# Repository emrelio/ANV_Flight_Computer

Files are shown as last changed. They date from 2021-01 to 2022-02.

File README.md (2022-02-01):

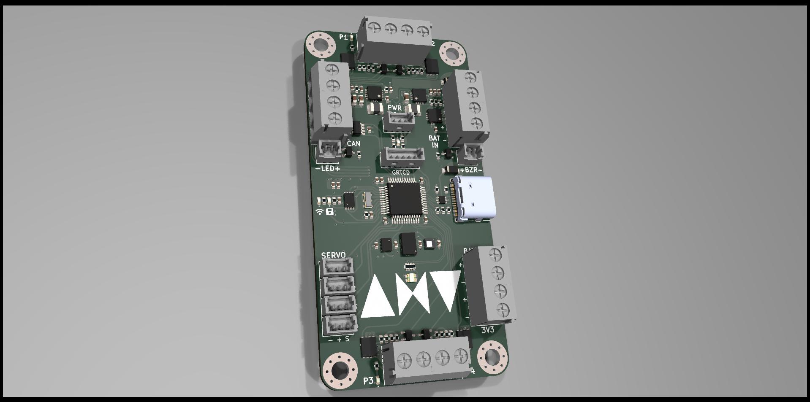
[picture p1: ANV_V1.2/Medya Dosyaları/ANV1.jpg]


Flight computer design for experimental model rocket flights.

I design this PCB for TVC of low power rockets.

Specs:

3-12V battery input,
  
Reverse battery protection,
  
3.3V and 5V switching regulators,
  
One main arm switch connector to cut all the power from the board,
  
Magnetic Switch connector for activation,
  
4, high current logic outputs,
  
All high current outputs have feedback for continuity detection,
  
4, 5v Servo outputs,
  
1,  LED and 1, active Buzzer connector,
  
1, RGB LED for notification,
  
ARM MCU,
  
Battery voltage and current sensors,
  
2, barometer from different brands for reliability,
  
9 DOF IMU,
  
4MB of memory for data logging,
  
Type-C connector for reading logged data,
  
433mHz LoRa for long-range wireless communication with U.FL connection,
  
Notification LED's for memory write and wireless communication,
  
Notification LED's for each high current outputs,
  
Screw terminal connector for power in-outs,
  
CAN-Bus connector for expansions in future,
  
M3 screw holes are connected to (BATT+, BATT-(GND), CAN-H, CAN-L).

Designed in KiCAD nightly.

Log:
  
Hall effect sensor out pin needs pull-up resistor, not pull-down. So It doesn't work.  
3.3V regulator acting abnormally. I might overheated it while soldering. Will try it on another board.  
IMU and Barometers are working.  
USB VCP is working.  
Current sensor is working.  
Mosfet feedback is working.  
Flash memory is working, logging algorithm is ready.  
Servo is working with integrated 5V regulator. Voltage might drop on load.  
  
To-Do :

Lora  
Can-Bus

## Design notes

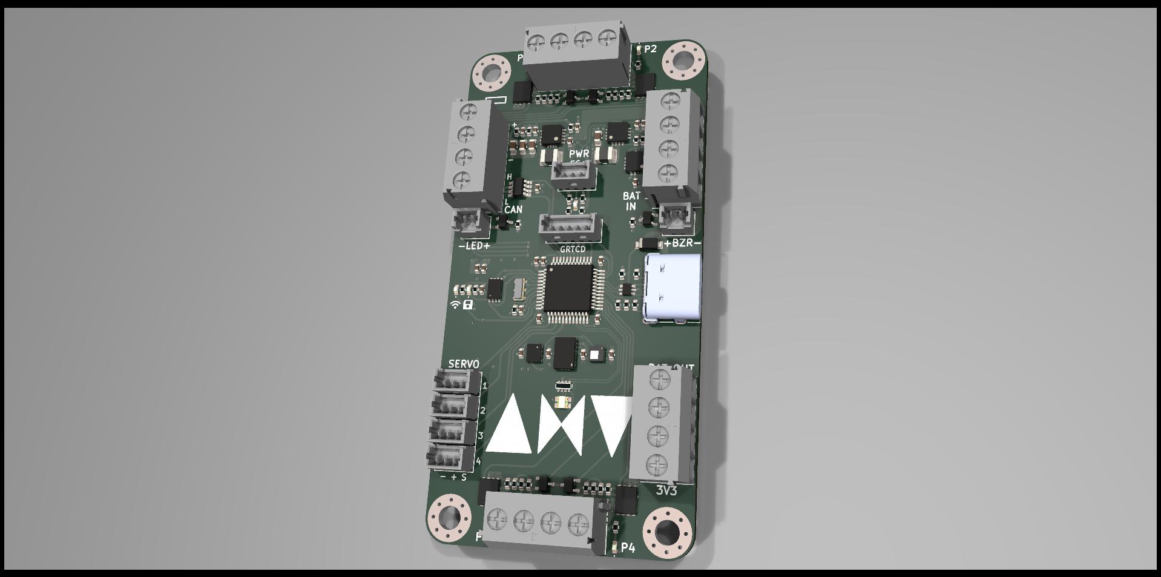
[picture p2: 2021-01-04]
ANV_V1.2/Medya Dosyaları/ANV2.jpg

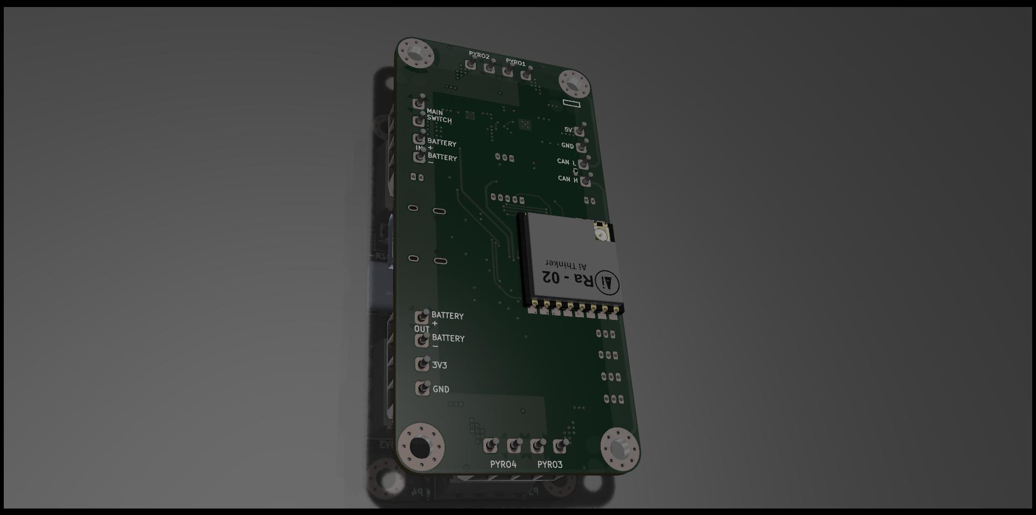
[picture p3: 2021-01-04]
ANV_V1.2/Medya Dosyaları/ANV3.jpg

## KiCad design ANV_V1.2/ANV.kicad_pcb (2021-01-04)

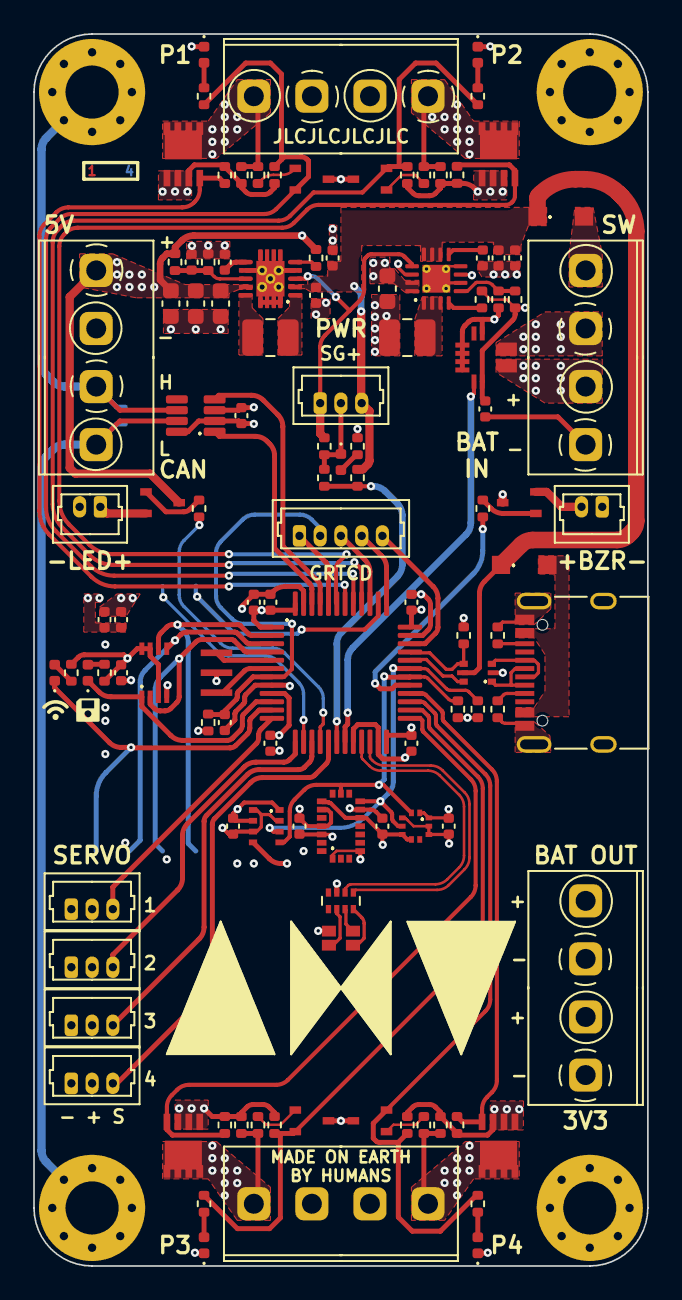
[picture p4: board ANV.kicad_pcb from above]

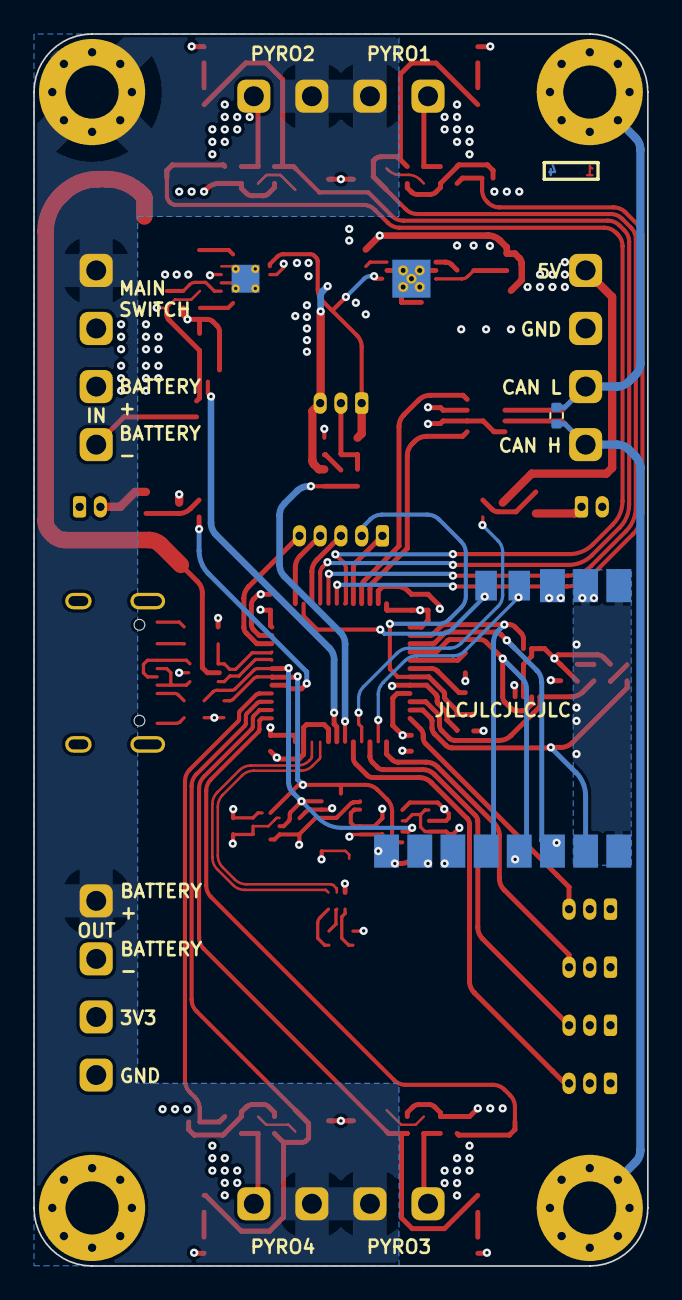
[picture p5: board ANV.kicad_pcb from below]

Board: 4 copper layers, 37.0 x 74.3 mm, 128 parts (2 on the bottom side), 83 nets.

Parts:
C1, C3, C7, C13, C14, C15, C16, C17, C18, C19, C20, C21, C23, C24, C25, C26, C27: 100nF; C_0402_1005Metric
C2, C4, C5: 10uF; C_0402_1005Metric
C6: 390pF; C_0402_1005Metric
C8: 10pF; C_0402_1005Metric
C9, C10, C11, C12: 22uF; C_0603_1608Metric
D1, D9: diode; D_SOD-123F
D2: flash; LED_0402_1005Metric
D3: pyro1; LED_0402_1005Metric
D4: pyro2; LED_0402_1005Metric
D5: pyro3; LED_0402_1005Metric
D6: pyro4; LED_0402_1005Metric
D7: 3v3; LED_0402_1005Metric
D8: RGB_Led; LED_LiteOn_LTST-C19HE1WT
D10: lora; LED_0402_1005Metric
H1: L; MountingHole_3.2mm_M3_Pad_Via
H2: H; MountingHole_3.2mm_M3_Pad_Via
H3: GND; MountingHole_3.2mm_M3_Pad_Via
H4: pwr; MountingHole_3.2mm_M3_Pad_Via
J1: programlama; Molex_PicoBlade_53047-0510_1x05_P1.25mm_Vertical
J2: Batt; 3.5mm_01x02_Screw_Terminal
J3: Sw; 3.5mm_01x02_Screw_Terminal
J4: USB_C_Receptacle_USB2.0; USB_C_Receptacle_XKB_U262-16XN-4BVC11
J5: switch/hallEffect; Molex_PicoBlade_53047-0310_1x03_P1.25mm_Vertical
J6: buzzer; Molex_PicoBlade_53047-0210_1x02_P1.25mm_Vertical
J7: 5v; 3.5mm_01x02_Screw_Terminal
J8: canbus; 3.5mm_01x02_Screw_Terminal
J9: led; Molex_PicoBlade_53047-0210_1x02_P1.25mm_Vertical
J10: pyro1; 3.5mm_01x02_Screw_Terminal
J11: pyro2; 3.5mm_01x02_Screw_Terminal
J12: pyro3; 3.5mm_01x02_Screw_Terminal
J13: pyro4; 3.5mm_01x02_Screw_Terminal
J14: servo1; Molex_PicoBlade_53047-0310_1x03_P1.25mm_Vertical
J15: servo2; Molex_PicoBlade_53047-0310_1x03_P1.25mm_Vertical
J16: batt; 3.5mm_01x02_Screw_Terminal
J17: 3v; 3.5mm_01x02_Screw_Terminal
J18: servo3; Molex_PicoBlade_53047-0310_1x03_P1.25mm_Vertical
J19: servo4; Molex_PicoBlade_53047-0310_1x03_P1.25mm_Vertical
L1: 1uH; L_1008_2520Metric
L2: 2.2uH; L_1008_2520Metric
LOGO1: anv; .A.N.V._Logo
LOGO2: rf; wifi
LOGO3: save; floppy
Q1, Q2, Q3, Q4: SE20N110; Vishay_PowerPAK_1212-8_Single
Q5, Q6, Q7, Q8, Q9, Q10: BC817W; SOT-323_SC-70
R1, R11: 100k; R_0402_1005Metric
R2: 30k; R_0402_1005Metric
R3, R4: 5k1; R_0402_1005Metric
R7, R12, R14, R15, R16, R17, R18, R19, R20, R21, R26, R27, R28, R29: 10k; R_0402_1005Metric
R8: 1k5; R_0402_1005Metric
R9, R39: 1m; R_0402_1005Metric
R10: 110k; R_0402_1005Metric
R13, R22, R23, R24, R25, R30, R31, R32, R33, R34, R35, R36, R45: 1k; R_0402_1005Metric
R37, R38: 4k7; R_0402_1005Metric
R40: 562k; R_0402_1005Metric
R41: 180k; R_0402_1005Metric
R44: 120r; R_0402_1005Metric
RN1: 1k; R_Array_Concave_4x0402
U1: ACS711xEXLT-15AB; Allegro_QFN-12-10-1EP_3x3mm_P0.5mm
U2: USBLC6-2P6; SOT-666
U3: TLV62130ARGTR; VQFN-16-1EP_3x3mm_P0.5mm_EP1.68x1.68mm_ThermalVias
U4: TPS63060; Texas_S-PWSON-N10_ThermalVias
U5: STM32F302C8Tx; LQFP-48_7x7mm_P0.5mm
U6: W25X40CLUXIG; DFN-8-1EP_3x2mm_P0.5mm_EP1.3x1.5mm
U7: LPS22HBTR; LPS22HB
U8: BMP280; Bosch_LGA-8_2x2.5mm_P0.65mm_ClockwisePinNumbering
U9: BMX055
U11: MAX3051; SOT-23-8
U12: Ai-Thinker-Ra-02; Ai-Thinker-Ra-01-LoRa
Y1: 8mHz; Resonator_SMD_muRata_CSTxExxV-3Pin_3.0x1.1mm

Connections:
+3V3: C1.1, C10.1, C14.2, C15.2, C16.2, C17.2, C18.2, C19.2, C20.1, C21.1, C23.2, C24.2, C25.2, C26.2, C27.2, D8.2 (VCC), J17.2, L2.2, Q5.3 (C), Q6.3 (C), Q9.3 (C), Q10.3 (C), R8.1, R11.1, R12.1, R13.1, R36.1, R37.1, R38.1, R40.1, R45.1, U1.10 (VCC), U3.7 (FSW), U3.14 (VOS), U5.1 (VBAT), U5.9 (VDDA), U5.24 (VDD), U5.36 (VDD), U5.48 (VDD), U6.3 (IO2), U6.7 (IO3), U6.8 (VCC), U7.1 (VDD_IO), U7.5 (SDO), U7.6 (CS), U7.10 (VDD), U8.2 (CSB), U8.6 (VDDIO), U8.8 (VDD), U9.3 (VDD), U9.7 (PS), U9.13 (VDDIO), U11.3 (VDD), U12.3 (VDD)
+5V: C9.1, C11.1, C12.1, J7.1, J14.2, J15.2, J18.2, J19.2, Q7.3 (C), Q8.3 (C), R9.1, R39.1, U4.9 (VOUT)
A0: D2.1 (K), U5.10 (PA0), U6.1 (~CS)
A1: D10.1 (K), U5.11 (PA1), U12.15 (~NSS)
A2: J14.3, U5.12 (PA2)
A3: J15.3, U5.13 (PA3)
A5: J18.3, U5.15 (PA5)
A6: R31.1, U5.16 (PA6)
A7: J19.3, U5.17 (PA7)
A8: R30.1, U5.29 (PA8)
A9: R37.2, U5.30 (PA9), U7.2 (SCL), U8.4 (SCK), U9.9 (SCX)
A10: R38.2, U5.31 (PA10), U7.4 (SDA), U8.3 (SDI), U9.11 (SDX)
A15: U5.38 (PA15), U12.5 (DIO0)
B0: R1.1, R2.2, U5.18 (PB0)
B1: U1.9 (VIOUT), U5.19 (PB1)
B3: J1.3, U5.39 (PB3)
B4: Q6.2 (E), R27.2, R33.1, U5.40 (PB4)
B5: Q5.2 (E), R26.2, R32.1, U5.41 (PB5)
B6: Q1.4 (G), R14.2, U5.42 (PB6)
B7: Q2.4 (G), R15.2, U5.43 (PB7)
B10: RN1.2 (R2.1), U5.21 (PB10)
B11: RN1.1 (R1.1), U5.22 (PB11)
B12: Q3.4 (G), R16.2, U5.25 (PB12)
B13: Q9.2 (E), R28.2, R34.1, U5.26 (PB13)
B14: Q10.2 (E), R29.2, R35.1, U5.27 (PB14)
B15: Q4.4 (G), R17.2, U5.28 (PB15)
Batt_+: C2.1, C3.1, C4.1, C5.1, D1.1 (K), D9.1 (K), J5.3, R1.2, U2.5 (VBUS), U3.10 (AVIN), U3.11 (PVIN), U3.12 (PVIN), U4.2 (VIN)
Batt_Pyro: D9.2 (A), H4.1, J3.2, J10.1, J11.2, J12.2, J13.1, J16.2
C13: U5.2 (PC13), U6.6 (CLK), U12.12 (SCK)
C14: U5.3 (PC14), U6.5 (DI(IO0)), U12.14 (MOSI)
C15: U5.4 (PC15), U6.2 (DO(IO1)), U12.13 (MISO)
GND: C1.2, C2.2, C3.2, C4.2, C5.2, C6.1, C7.2, C8.2, C9.2, C10.2, C11.2, C12.2, C13.1, C14.1, C15.1, C16.1, C17.1, C18.1, C19.1, C20.2, C21.2, C23.1, C24.1, C25.1, C26.1, C27.1, D3.1 (K), D4.1 (K), D5.1 (K), D6.1 (K), D7.1 (K), H3.1, J1.1, J2.1, J4.A1 (GND), J4.A12 (GND), J4.B1 (GND), J4.B12 (GND), J4.S1 (SHIELD), J5.2, J6.1, J7.2, J9.2, J14.1, J15.1, J16.1, J17.1, J18.1, J19.1, Q1.1 (S), Q1.2 (S), Q1.3 (S), Q2.1 (S), Q2.2 (S), Q2.3 (S), Q3.1 (S), Q3.2 (S), Q3.3 (S), Q4.1 (S), Q4.2 (S), Q4.3 (S), R2.1, R3.2, R4.2, R7.1, R10.2, R14.1, R15.1, R16.1, R17.1, R18.1, R19.1, R20.1, R21.1, R26.1, R27.1, R28.1, R29.1, R41.2, RN1.3 (R3.1), U1.3 (GND), U1.5 (NC), U1.6 (NC), U1.7 (NC), U1.8 (NC), U2.2 (GND), U3.6 (AGND), U3.8 (DEF), U3.15 (PGND), U3.16 (PGND), U3.17 (THERMAL_PAD), U4.4 (PS/SYNC), U4.7 (GND), U4.11 (PGND), U5.8 (VSSA), U5.20 (PB2), U5.23 (VSS), U5.35 (VSS), U5.44 (BOOT0), U5.47 (VSS), U6.4 (GND), U7.3 (-), U7.8 (GND), U7.9 (GND), U8.1 (GND), U8.5 (SDO), U8.7 (GND), U9.4 (GNDA), U9.6 (GNDIO), U9.12 (SDO2), U9.17 (SDO1), U9.20 (CSB3(magnet)), U11.2 (GND), U11.8 (RS), U12.1 (GND), U12.2 (GND), U12.9 (GND), U12.16 (GND), Y1.2
unnamed: C6.2, U3.9 (SS/TR)
unnamed: C7.1, U4.6 (VAUX)
unnamed: C8.1, R9.2, R10.1, U4.8 (FB)
unnamed: D1.2 (A), J4.A4 (VBUS), J4.A9 (VBUS), J4.B4 (VBUS), J4.B9 (VBUS)
unnamed: D2.2 (A), R13.2
unnamed: D3.2 (A), R32.2
unnamed: D4.2 (A), R33.2
unnamed: D5.2 (A), R34.2
unnamed: D6.2 (A), R35.2
unnamed: D7.2 (A), R36.2
unnamed: D8.1 (B), RN1.6 (R3.2)
unnamed: D8.3 (G), RN1.7 (R2.2)
unnamed: D8.4 (R), RN1.8 (R1.2)
unnamed: D10.2 (A), R45.2
unnamed: J2.2, U1.1 (IP+)
unnamed: J3.1, U1.2 (IP-)
unnamed: J4.A5 (CC1), R3.1
unnamed: J4.A6 (D+), J4.B6 (D+), U2.3 (I/O2)
unnamed: J4.A7 (D-), J4.B7 (D-), U2.1 (I/O1)
unnamed: J4.B5 (CC2), R4.1
unnamed: L1.1, U4.1 (L1)
unnamed: L1.2, U4.10 (L2)
unnamed: L2.1, U3.1 (SW), U3.2 (SW), U3.3 (SW)
unnamed: Q5.1 (B), R22.2
unnamed: Q6.1 (B), R23.2
unnamed: Q7.1 (B), R30.2
unnamed: Q8.1 (B), R31.2
unnamed: Q9.1 (B), R24.2
unnamed: Q10.1 (B), R25.2
unnamed: R11.2, U3.4 (PG)
unnamed: R39.2, U4.5 (PG)
unnamed: R40.2, R41.1, U3.5 (FB)
unnamed: U5.5 (PF0), Y1.1
unnamed: U5.6 (PF1), Y1.3
Reset: C13.2, J1.2, R12.2, U5.7 (NRST)
SWCLK: J1.4, U5.37 (PA14)
SWDIO: J1.5, U5.34 (PA13)
USB_D+: R8.2, U2.4 (I/O2), U5.33 (PA12)
USB_D-: U2.6 (I/O1), U5.32 (PA11)
buzzer_out: J6.2, Q7.2 (E)
can_H: H2.1, J8.2, R44.1, U11.7 (CANH)
can_L: H1.1, J8.1, R44.2, U11.6 (CANL)
canrx: U5.45 (PB8), U11.4 (RXD)
cantx: U5.46 (PB9), U11.1 (TXD)
en: J5.1, R7.2, U3.13 (EN), U4.3 (EN)
led_out: J9.1, Q8.2 (E)
lora_reset: U5.14 (PA4), U12.4 (~RESET)
pyro1_out: J10.2, Q1.5 (D), R18.2, R22.1
pyro2_out: J11.1, Q2.5 (D), R19.2, R23.1
pyro3_out: J12.1, Q3.5 (D), R20.2, R24.1
pyro4_out: J13.2, Q4.5 (D), R21.2, R25.1
